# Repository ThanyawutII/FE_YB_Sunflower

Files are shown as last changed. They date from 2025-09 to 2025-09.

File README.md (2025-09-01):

# YB-SUNFLOWER-Future-Engineers🌻✨
### ***We Are Team YB-SUNFLOWER***

</p>
<p align="center">
  
</p>

<p align="center">
 by Yothinburana School

</p>

# Content
`3DModels` This folder includes the 3D design of the vehicle and the rendered model of the vehicle.

`Document (PDF form)` In this folder, we have included a Word document that reorganizes the information from GitHub. It has been converted into a PDF for printing on A4 paper.

`FlowChart` This folder includes diagrams showing the logic and sequence of the robot's control program, highlighting how it processes inputs and controls movements during missions.

`Others` Other essential photos like, work schedule, and robot assemble gif.

`Program` This folder includes all the codes that are used in the WRO 2025 Future Engineers Category and all the programming flowcharts.

`Robot-Photos` This folder contains photos of the vehicle from all perspectives, including side and bottom views.

`Schemes` This folder contains one or more schematic diagrams in JPEG, PNG, or PDF format that depict the electromechanical components of the vehicle. These diagrams illustrate all the elements, including electronic components and motors, and show how they are interconnected.

`Team-Photos` This folder includes photos of the team participating in the WRO 2025 Future Engineers Category.

`Videos` This folder contains YouTube links that show how the robot operates to complete both missions.

`Readme` This Readme contain 3 parts.

  - [About Us](#part-1-about-us)
  - [Mechanical Design](#part-2-mechanical-design)
  - [Obstacle Management](#part-3-obstacle-management)

</p>

# **Part 1: About Us**

## **This is our team.**
Our team name, YB-SUNFLOWER, carries a meaningful story. The word “Sunflower” comes from one of our seniors, Tawan (ตะวัน). In Thai, “sunflower” is ทานตะวัน, which is directly connected to his name. Since 2023, he has inspired us to join the Future Engineers Competition, always supporting us and giving guidance from outside the team. To honor the role he played in motivating us, we included “Sunflower” in our team name. This year is even more special, because for the first time, he is actually competing together with us as part of the team.
 
 <hr>

### **Team History** 
 
 We are **YB-SUNFLOWER**, team from Bangkok, Thailand. We are a part of YB-Robot club from Yothinburana School with our mentor, Punnapon Tanasnitikul. This is our club website https://ybrobot.club/. The club was established in 2009 with the first name being “YB Dream Team”. Last year, we also attend in WRO 2024 that took place in Türkiye.

 This is the first WRO international award in 2010.
  <p align="center">
    
</p>
  </p>
  </p>
This is the second WRO international award in 2011.
 <p align="center">
    
</p>
  </p> 
  </p>

This is the latest WRO international award in 2024 (13th place).  
 <p align="center">
    
</p>
Currently in 2025, we are a part of YB Robot Team. Our senior brought this team name to global recognition, so there is a responsibility since our senior perform excellently. We are hoping to keep this name on the winning streak and make them proud. </p>
  </p>
  </p>
  <hr>

### **Our Team**
   The team consists of 2 intimate friends and 1 of our senior, 'Tawan'. Pawit Nateenantasawasd, Thanyawut Krittikanon, and Natapol Chusang. We have known each other for four years since 2021, forming a strong bond that enhances our collaborative efforts. We first met in high school, being in robot club, competing in many robot competitions together, and sharing our robotic knowledge. Much of what we know today has been learned from the experiences of our seniors in out team, who have taught us valuable lessons and helped shape who we are now.

   Last 2 years, with great enthusiasm and high spirits, we joined Future Engineers twice. Reaching the international round was already a great honor, but we were soon to realize that in order to win, one needs more than just enthusiasm. Our mistakes led us take the 8th and 13th position, a respectable position indeed. 

   This year, we are back with greater confidence, and wiser from past experiences. We honed our strategies and prepared extensively. We fixed every mistake we have done last 2 years. Being back at this competition make us want to ensure the best outcome, and we are here to make everyone proud.  

<p align="center">
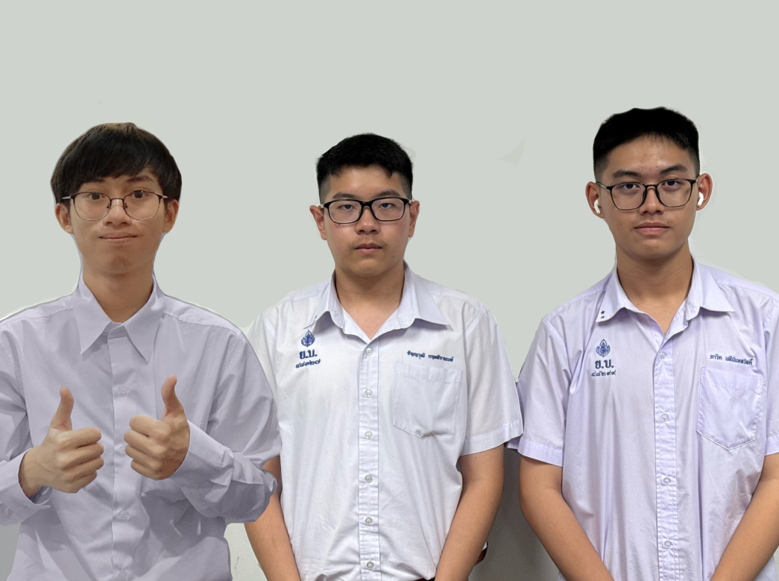
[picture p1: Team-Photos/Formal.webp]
    
</p>

<hr>
There are three members in our team, all extremely focused and dedicated to their positions, performing functions as follows: 
 
#### 1. Thanyawut Krittikanon – Robot Designer
<p align="center">
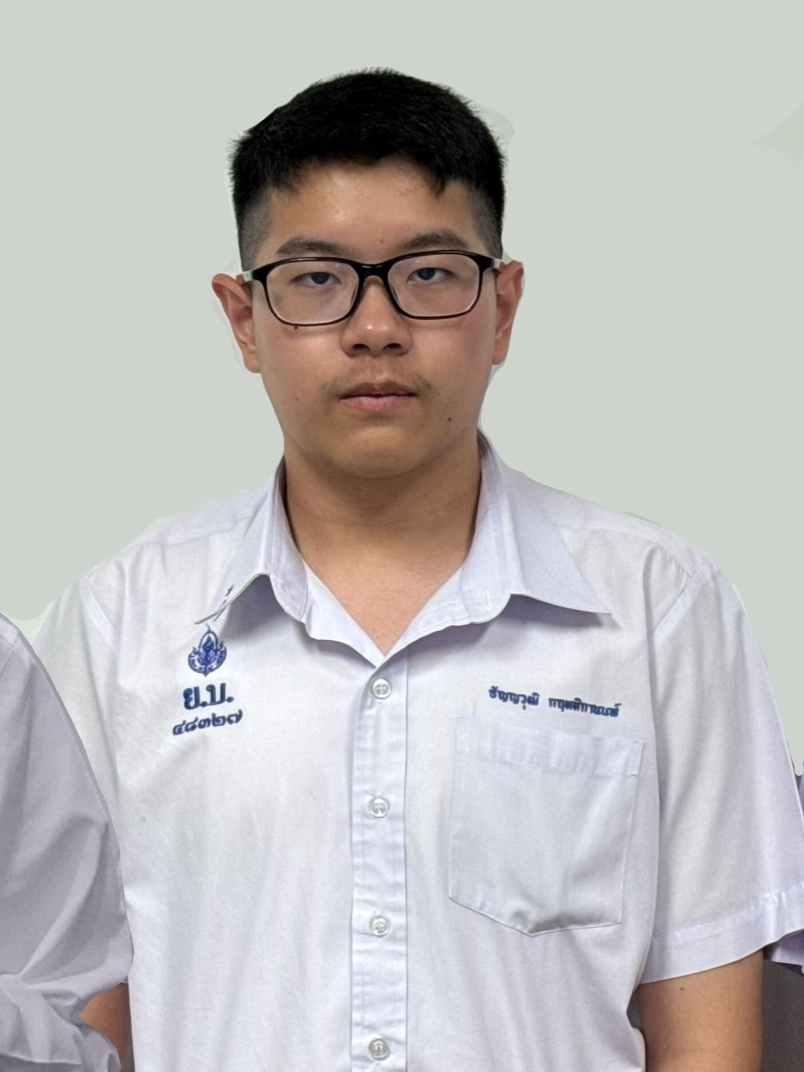
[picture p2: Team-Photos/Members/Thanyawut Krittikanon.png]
    
</p>
Thanyawut is known in our team as **The God of Fusion**, with outstanding skills in 3D design and modeling. His expertise in creating precise and creative robot designs makes him a crucial part of our team. With his talent, he can turn our ideas into detailed models that guide the building process and bring our concepts to life.

#### 2. Pawit Nateenantasawasd – Document Designer and Electrician 
<p align="center">
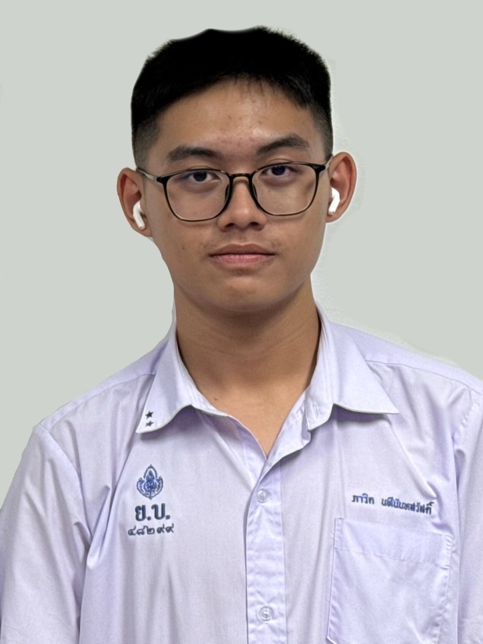
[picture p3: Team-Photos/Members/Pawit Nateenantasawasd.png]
    
</p>
I am Pawit, the document designer of our team. My role is to make sure that everything we present — from reports to presentations — is clear, well-structured, and professional. I enjoy transforming complex ideas into something simple and easy to understand, while also giving it a creative and polished design. Besides designing documents, I also have strong coding skills in multiple languages such as C++, C, Python, Micropython, and HTML, which allow me to contribute to the technical side of our work.

#### 3. Natapol Chusang - Programmer
<p align="center">
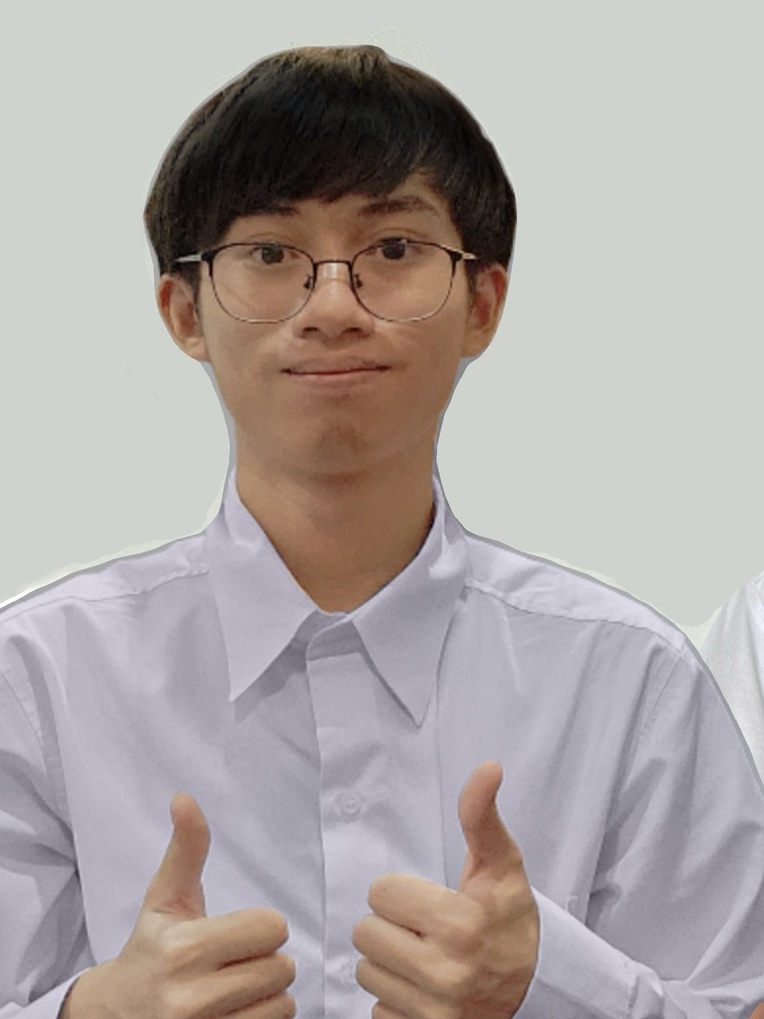
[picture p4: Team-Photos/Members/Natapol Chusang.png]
    
</p>
Natapol is our master programmer, and sometimes we joke that he’s not even human because of how effortlessly he can code anything. From bad-looking robot to advanced systems, he can take on any programming challenge that comes his way. His ability to quickly understand problems and turn them into working solutions makes him a key part of our team’s success. With his skills, even the most complex systems feel possible to build — it’s like there’s no code in the world he cannot write.

</p>
<hr>

### **Our Vision and Goal**

We want to create a robot that can operate similarly to a self-driving car, with the hope of integrating it with an actual automobile. This competition is a step toward our future goal of helping our country and inventing new things. Additionally, via participating in this competition, we have developed and learned numerous skills like collaboration, imagination, and foresight. We also desired to meet new friends in order to exchange knowledge. Furthermore, we intend to utilize the experience we have obtained from this tournament to better ourselves and mentor our junior at school.

<hr>

# **Part 2: MECHANICAL DESIGN**

## Robot's Chassis



The robot chassis design consists mainly of the 3D printed parts, which provide a strong support for all the hardware and electronics devices. Each element is custom-designed to meet our specific requirements and interlocks seamlessly to create a lightweight yet resilient structure. Modification and extension of the orthotics and bambulab 3D-printed chassis is made easily due to its modular construction. It is designed to house the motors, electronic circuitry, and battery while enhancing thermal management and balanced weight distribution for efficient operation. This strategy not only allows for fast modeling and changes in design, but it also makes it easy if an operational change requires that some parts should be removed or replaced with better ones as the robot matures. [All the 3D printable models can be found here](https://github.com/Book2009/Nocturnalist-Future-Engineers/tree/main/3D_Models).

<hr>

### Main Base

<table align="center">
  <tr>
    <td align="center">
      

  <p><a href="https://github.com/Book2009/FE-NOC/blob/main/3D_Models/Main%20Base.stl" target="_blank">Click here to view 3D model.</a></p>
  </tr>
</table>

The main base provides the foundation for creating all other parts. It has cylindrical extensions meant to attach the servo and motor too — designed with LEGO connectors in mind, as opposed to clunky black pegs. Also detailed are the openings to accommodate both differential gear and regular gears so they do not hit the base when trying to rotate. One is a specially designed slot to work with this 3D-printed differential gear mount. The front part is cut out deeper so the servo for steering fits inside and has no problems to spin freely. This design allows to move effectively and optics in the small space of the robot.

<hr>

### Support Base

<table align="center">
  <tr>
    <td align="center">
      

  <p><a href="https://github.com/Book2009/FE-NOC/blob/main/3D_Models/Support%20Plate.stl" target="_blank">Click here to view 3D model.</a></p>
  </tr>
</table>

The purpose of this component is to reinforce the main base securing attachments more firmly. It serves as an additional foundation to mount objects and 3D models, ensuring stability and strength in the overall structure.

<hr>

### C Clip

<table align="center">
  <tr>
    <td align="center">
      

  <p><a href="https://github.com/Book2009/FE-NOC/blob/main/3D_Models/C%20Clip%20x4.stl" target="_blank">Click here to view 3D model.</a></p>
  </tr>
</table>

This component functions as a stabilizing element, similar to a nut, preventing objects from shifting or moving out of place. The open, C-shaped design allows it to be easily positioned around shafts or other components, ensuring they remain securely fixed while maintaining flexibility for adjustments when needed.

<hr>

### Differential Gear Mount

<p align="center">

</p>

<table align="center">
  <tr>
    <td align="center">
      Left
      <p><details>
  <summary>Left Differential Gear Mount</summary>

  <p><a href="https://github.com/Book2009/FE-NOC/blob/main/3D_Models/Left%20Differential%20Gear%20Mount.stl" target="_blank">Click here to view 3D model.</a></p>

</details></p>
    </td>
    <td align="center">
      Right
      <p><details>
  <summary>Left Differential Gear Mount</summary>

  <p><a href="https://github.com/Book2009/FE-NOC/blob/main/3D_Models/Right%20Differential%20Gear%20Mount.stl" target="_blank">Click here to view 3D model.</a></p>

</details></p>
    </td>
  </tr>
</table>

This component is very important for supporting the differential gear firmly and creating solidity to the drivetrain of our robot. Among the basic choices that we made during the work on the robot design, one of the key decisions was to use as few bolts and nuts as possible. This reduction in weight is achieved by using ABS plastic filament instead of steel, which is significantly lighter. This choice not only decreases the overall weight but also simplifies the assembly by requiring fewer additional elements and connections.

<p align="center">


A lighter robot just provides enhanced mobility and more efficiency, which is a crucial factor given the requirements of competitively in the competition. In order to attain a most stringent connection to the main base an interlocking joint was implemented. This design helps in assembling by minimizing the use of conventional fasteners during the construction process. 

<p align="center">
   
  
From this connection, we developed cylindrical formings which work more like bolts, used to place the parts in right position as well as fix them in place.

<p align="center">


Made for added security, precision grooves feature with special C-clips that serve as a replacement for nuts, designed to fit seamlessly. These C-clips are held firmly in place within specially designed grooves that prevent any movement. The groove area has a smaller diameter than the other sections, which ensures a tight fit, preventing any up-and-down motion. The only way to release the C-clip would be to pull it sideways, making the design stable and secure.

<p align="center">


<hr>

### Power Tray

<table align="center">
  <tr>
    <td align="center">
      

  <p><a href="https://github.com/Book2009/FE-NOC/blob/main/3D_Models/Power%20Tray.stl" target="_blank">Click here to view 3D model.</a></p>
  </tr>
</table>

This is the part that holds the 11.1V battery, which is easily removable for charging. This also serves to securely mount the step-down module in place. The raised portion at the back forms a stable platform for mounting the microcontroller board. Hence, this design optimizes the layout by keeping the important electronics of the best organization in space and providing stability.

<hr>

### Servo Bracket

<table align="center">
  <tr>
    <td align="center">
      

  <p><a href="https://github.com/Book2009/FE-NOC/blob/main/3D_Models/Servo%20Bracket.stl" target="_blank">Click here to view 3D model.</a></p>
  </tr>
</table>

This component is intended for firm attachment of a servo motor accompanied by an ultrasonic sensor that is to be used in rotation. The design incorporates cylindrical spigots so as to eliminate the use of black pins which are used to fasten the servo motor fabricated for Lego use. With this arrangement, the sensor movement is stable, well positioned and rigid within the system that improves the overall utility of the sensor.

<hr>

### Camera Plate

<table align="center">
  <tr>
    <td align="center">
      

  <p><a href="https://github.com/Book2009/FE-NOC/blob/main/3D_Models/Camara%20Plate.stl" target="_blank">Click here to view 3D model.</a></p>
  </tr>
</table>

This component is designed to attach to the back of the camera, providing a mounting point that enables it to be securely connected to other components.

<hr>

### Handle
<p align="center">

</p>

<table align="center">
  <tr>
    <td align="center">
      Left
      <p><details>
  <summary>Left Side Handle Support</summary>

  <p><a href="https://github.com/Book2009/FE-NOC/blob/main/3D_Models/Left%20Side%20Handle%20Support.stl" target="_blank">Click here to view 3D model.</a></p>

</details></p>
    </td>
    <td align="center">
      Center
      <p><details>
  <summary>Upper Handle Bracket</summary>

  <p><a href="https://github.com/Book2009/FE-NOC/blob/main/3D_Models/Upper%20Handle%20Bracket.stl" target="_blank">Click here to view 3D model.</a></p>

</details></p>
    </td>
 <td align="center">
      Right
      <p><details>
  <summary>Right Side Handle Support</summary>

  <p><a href="https://github.com/Book2009/FE-NOC/blob/main/3D_Models/Right%20Side%20Handle%20Support.stl" target="_blank">Click here to view 3D model.</a></p>

</details></p>
    </td>
  </tr>
</table>

This handle is an important part as it allows the robot to be safely lifted, especially at times of high speeds. Should it happen that the robot malfunctions or does not act as intended, reaching down quickly to grasp it is practically impossible and could cause unintentional damage by tugging at sensitive pieces, including wires. With the handle, the robot can be raised safely and securely with minimal risk of mishandling.

<hr>

### Gyro-Camara Mount

<table align="center">
  <tr>
    <td align="center">
      

  <p><a href="https://github.com/Book2009/FE-NOC/blob/main/3D_Models/Gyro-Camara%20Mount.stl" target="_blank">Click here to view 3D model.</a></p>
  </tr>
</table>

This component is mounted to the handle and serves as the mounting area for the camera, which is secured through the camera plate. It allows the camera to tilt forward or backward, enabling flexible adjustments to capture the best angle for the robot's operations. Additionally, it offers a stable attachment point for the gyro sensor, ensuring accurate orientation and sensor alignment. The gyro mount is positioned around the middle top of the robot to achieve the most accurate output, while the camera mount is placed at the back to ensure precise object detection.

<hr>

### Steering Module
<p align="center">

</p>

<table align="center">
  <tr>
    <td align="center">
      Left
      <p><details>
  <summary>Bottom Steering Mount</summary>

  <p><a href="https://github.com/Book2009/FE-NOC/blob/main/3D_Models/Bottom%20Steering%20Mount.stl" target="_blank">Click here to view 3D model.</a></p>

</details></p>
    </td>
    <td align="center">
      Center
      <p><details>
  <summary>Steering Linkage Arm</summary>

  <p><a href="https://github.com/Book2009/FE-NOC/blob/main/3D_Models/Steering%20Linkage%20Arm.stl" target="_blank">Click here to view 3D model.</a></p>

</details></p>
    </td>
 <td align="center">
      Right
      <p><details>
  <summary>Top Steering Mount</summary>

  <p><a href="https://github.com/Book2009/FE-NOC/blob/main/3D_Models/Top%20Steering%20Mount.stl" target="_blank">Click here to view 3D model.</a></p>

</details></p>
    </td>
  </tr>
</table>

<table align="center">
  <tr>
    <td align="center">
      Left
      <p><details>
  <summary>Steering Arm</summary>

  <p><a href="https://github.com/Book2009/FE-NOC/blob/main/3D_Models/Steering%20Arm.stl" target="_blank">Click here to view 3D model.</a></p>

</details></p>
    </td>
 <td align="center">
      Right
      <p><details>
  <summary>Steering Arm Support</summary>

  <p><a href="https://github.com/Book2009/FE-NOC/blob/main/3D_Models/Steering%20Arm%20Support.stl" target="_blank">Click here to view 3D model.</a></p>

</details></p>
    </td>
  </tr>
</table>

- #### **Bottom Steering Mount**

Its primary function is to ensure that both steering arms are aligned at the same angle during turns, providing precise and synchronized steering. It connects to the steering linkage arm, which is linked to the servo motor, allowing controlled movement and adjustments to the wheel angles. Additionally, we have designed a mounting point at the front of this component for a light sensor.

- #### **Steering Linkage Arm**

Its main function is to connect to the servo motor and control the steering direction of the robot.

- #### **Top Steering Mount**

Its primary function is to reinforce the bottom steering module, providing additional strength and stability to the steering structure. Additionally, we've designed a mount for an ultrasonic sensor

- #### **Steering Arms**

Its main function is to keep the bottom and top steering mounts aligned with the front of the robot, ensuring stability and correct orientation. Additionally, it serves as the attachment point for the wheels. At the rear of this component, we've designed a large hole to fit a metal standoff or PCB support post, providing extra reinforcement to prevent breakage and enhance durability.
<p align="center">


- #### **Steering Arm Supports**

Its primary function is to provide additional support for the PCB mounting posts, which are made of metal and are insufficiently long.

<hr>

### Chassis

- #### **This is the appearance of chassis to show what our robot looks like without the components.**

<p align="center">


## Components

- #### **3D Printer**: Bambu Lab X1 Carbon by Bambu Lab
<image src="https://github.com/Book2009/FE-NOC/blob/main/Robot-Photos/Robot%20Parts/3D/3D%20Printer.png" width = "400">
The reasons that we use Bambu Lab X1-Carbon 3D printer because this printer is a high-performance 3D printer designed for precision and efficiency. It is equipped with advanced technology and features, making it suitable for professional use as well as hobbyist projects that require high-quality prints.

##### General Specifications

| Specification | Value |
|---|---|
| Build Volume | 256 × 256 × 256 mm³* |
| Nozzle | 0.4 mm Hardened Steel Included |
| Hotend | All-Metal |
| Max Hot End Temperature | 300 ℃ |
| Filament Diameter | 1.75 mm |
| Supported Filament | PLA, PETG, TPU, ABS, ASA, PVA, PET |
| Ideal for | PA, PC, Carbon/Glass Fiber Reinforced Polymer |

##### Build Plate Specifications

| Specification | Value |
|---|---|
| Build Plate Surface | Bambu Textured PEI Plate or Bambu Cool Plate (Pre-installed, Random, Both compatible with Micro Lidar) |
| Max Build Plate Temperature | 110℃@220V, 120℃@110V |

##### Tool Head Specifications

| Specification | Value |
|---|---|
| Max Speed | 500 mm/s |
| Max Acceleration | 20 m/s² |

##### Physical Dimensions

| Specification | Value |
|---|---|
| X1C Dimensions | 389 × 389 × 457 mm³ |
| Package Size (X1C) | 480 × 480 × 535 mm³ |
| Net Weight (X1C) | 14.13 kg |
| Gross Weight (X1C) | 18 kg |
| Package Size (X1C Combo) | 480 × 480 × 590 mm³ |
| Gross Weight (X1C Combo, AMS included) | 22.3 kg |

##### Electrical Requirements

| Specification | Value |
|---|---|
| Voltage | 100-240 VAC |
| Frequency | 50/60 Hz |
| Power Consumption | 1000W@220V, 350W@110V |

<hr>

- #### **Filament** : Acrylonitrile Butadiene Styrene or simply known as ***ABS**
<image src="https://github.com/Book2009/FE-NOC/blob/main/Robot-Photos/Robot%20Parts/3D/ABS%20Filament.png" width = "400">
ABS (acrylonitrile butadiene styrene) is probably the most common filament used in 3D printing. It is especially valuable in strong plastic parts that must remain resilient in the face of temperature swings. It is mainly used in FDM (fused deposition modeling) 3D printers. ABS is a thermoplastic polymer composed of three monomers: acrylonitrile, butadiene, and styrene. The material was first patented in the 1940s and very quickly gained popularity.

<hr><br>

### Movement Parts

- #### **Driving motor** : Power Functions Large-Motor made by LEGO™.
<image src="https://github.com/Book2009/FE-NOC/blob/main/Robot-Photos/Robot%20Parts/Movement/Motor.png" width = "400">
It's a simple motor, and we chose this motor because of its easy connection to our robot and its cost-effectiveness. This motor is small yet powerful and small power consumption. It is the perfect size for our robot comparing to other motor in the market which typically round on all side and need specific mounting bracket for example ZGA32RI. The motor comes with a dedicated port for Lego. So, we modified it to make it able to connect to the board. 

##### Electrical Specifications

| Specification | Value |
|---|---|
| Voltage | 9 V |

##### Mechanical Specifications

| Specification | Value |
|---|---|
| Speed | 390 rpm  |
| Maximum torque | 40 Ncm |

<hr>

- #### **Differential** : Technic, Gear Differential with Inner Tabs and Closed Center, 28 Bevel Teeth
<image src = "https://github.com/Book2009/FE-NOC/blob/main/Robot-Photos/Robot%20Parts/Movement/differential%20gear.png" width = "300"> <image src = "https://github.com/ThanyawutII/Test-2/blob/main/different.jpg" width = "400">

This part ensure that both wheels have the power from the motor, which makes the robot drive forward. This part has gear teeth on the side, which are connected to the gear we put on the motor earlier, and then we put 3 small gears inside the differential. The differential is attached to the main body using an axle from the wheel.

<hr>

- #### **Driving Motor with Differential Gear**
<image src="https://github.com/ThanyawutII/Test-2/blob/main/Screenshot_2024-11-16_223901-removebg-preview.png" width = "500">

After presenting the information and the reasons for selecting the motor and the differential gear, the next crucial step is to understand the outcomes resulting from the connection of these two components. This analysis aims to determine the speed and torque that the system can deliver, which are key factors in optimizing and enhancing the system's performance. Below are the calculation methods and the results derived from our analysis

#### **Step 1: Calculate the gear ratio**
<p>The gear ratio is determined by the ratio of the number of teeth on the input and output gears:</p>
<div class="equation">
    Gear Ratio = <sup>Number of teeth on input gear</sup> / <sub>Number of teeth on output gear</sub> = <sup>36</sup> / <sub>28</sub> = 1.2857
</div>

#### **Step 2: Calculate output RPM**
<p>The output RPM increases due to the gear ratio. To find the output RPM:</p>
<div class="equation">
    Output RPM = Input RPM × Gear Ratio = 390 × 1.2857 = 501.4 RPM
</div>

#### **Step 3: Calculate output torque**
<p>The torque decreases inversely proportional to the gear ratio. To find the output torque:</p>
<div class="equation">
    Output Torque = <sup>Input Torque</sup> / <sub>Gear Ratio</sub> = <sup>40</sup> / <sub>1.2857</sub> = 31.1 N·cm
</div>

#### **Final Results:**
<ul>
    <li><strong>Output RPM</strong>: ~501.4 RPM</li>
    <li><strong>Output Torque</strong>: ~31.1 N·cm</li>
</ul>

</body>
</html>

<hr>

- #### **Servo** : GEEKSERVO 2kg 360 Degrees Servo.
<image src="https://github.com/Book2009/FE-NOC/blob/main/Robot-Photos/Robot%20Parts/Movement/servo.png" width = "400">
We use this servo for steering the robot and employ an ultrasonic sensor for rotation. This servo is compatible with LEGO, making it easy and convenient to build the robot by just putting studs in the hole on the side. We like how you can connect two axles to the dual outputs on this servo so you can power two wheels or gears or mount the servo securely inside articulated limbs and other contraptions. Additionally, the gears inside these servos will 'slip' when the blocking load is too high instead of jamming, helping avoid damage to your servos and boards.

The wires are a standard servo pinout - 
-	Red - positive
-	Brown - negative
-	Yellow - data

##### Electrical Specifications

| Specification | Value |
|---|---|
| Working voltage | 3.3V~6V  |
| Rated voltage | 4.8V |
| Rated current | 200mA |
| Stall current | 700mA |
| Sliding current | 450mA |

<hr>

- #### **Front Wheel** : Lego Tire 43.2 x 22 ZR and Wheel 30.4mm D. x 20mm with No Pin Holes and Reinforced Rim
<image src = "https://github.com/ThanyawutII/Test/blob/main/Screenshot_2024-10-23_143240-removebg-preview.png" width = "200"> <image src = "https://github.com/ThanyawutII/Test/blob/main/56145-removebg-preview%20(1).png" width = "200">
  
  - #### **Rear Wheel** : Lego Tire 49.6 x 28 VR and Wheel 36.8mm D. x 26mm VR with Axle Hole
<image src = "https://github.com/ThanyawutII/Test-2/blob/main/S__5021716-removebg-preview.png" width = "200"> <image src = "https://github.com/ThanyawutII/Test-2/blob/main/S__5021714-removebg-preview.png" width = "200">

There are a lot of wheels to select. We chose this one because of it's size. If the wheels are too small, it reduces the speed due to the lack of rotation. But if the wheels are too big, it makes the robot slower and harder to control. With the combination of the motor and the wheels, the robot can maintain the speed we can control.

<hr><br>

### Controller

- #### **Microcontroller Board** : Arduino Mega 2560 R3

This part is like a brain of our body. Its job is to store all the program of our robot from the computer, every component in the robot comes through here. We chose this board because of its connection port, it contains tons of ports that we want such as 3 UART port. We used Arduino Uno last year, but the problem is there's not enough port for OpenMV and GY-25. But there's some disadvantage in this board. Because this board has a lot of connection port, it comes with weight and size. It's almost 2 times longer than the UNO. And that makes the robot long and heavy.

| Specification | Value |
|---|---|
| Microcontroller | ATmega2560 |
| Operating Voltage | 5V |
| Input Voltage (recommended) | 7-12V |
| Input Voltage (limit) | 6-20V |
| Digital I/O Pins | 54 (15 provide PWM output) |
| Analog Input Pins | 16 |
| DC Current per I/O Pin  | 20 mA |
| DC Current for 3.3V Pin | 50 mA |
| Flash Memory | 256 KB (8 KB used by bootloader) |
| SRAM | 8 KB |
| EEPROM | 4 KB |
| Clock Speed | 16 MHz |
| LED_BUILTIN | 13 |
| Length | 101.52 mm |
| Width | 53.3 mm |
| Weight | 37 g |

Additional information about UART:
UART operates by transmitting data as a series of bits, including a start bit, data bits, an optional parity bit, and stop bit(s). Unlike parallel communication, where multiple bits are transmitted simultaneously, UART sends data serially, one bit at a time. As the name reveals the protocol operates asynchronous which means that it doesn't rely on a shared clock signal. Instead, it uses predefined baud rates to determine the timing of data bits.



Our robot has serial1 and serial3, serial1 is connected to compass while serial3 is connected to OpenMV camera. They are connected to the UART port on the Arduino mega.

<hr>

- #### **Sensor Shield** : Gravity IO Sensor Shield for Arduino Mega Due

This part is an extension of the board. It is where ultrasonic, light sensors, button sensors, camera, compass, and servos go. It has a lot of connection pin which can be used for each component. But with that it also come with a very long design. Make it hard to design where to place it on robot.

| Specification | Value |
|---|---|
| Compatibility | Most Arduino shields |
| Compatible Boards | Arduino Mega boards, DFRobot megaADK, Arduino megaADK |
| Extended TTL Connection Pins | Four Serial ports |
| Prototyping Area | DIP prototyping area for additional modules or components |
| Xbee Slots | 3 |
| microSD Slot | 1 |
| Power Switch | Between Arduino Mega or external power |
| Size | 125 x 57 mm (4.92 x 2.24") |

<hr>

- #### **Motor Shield** : Gravity 2x2A Motor Shield for Arduino Twin

This part is also an extension of the board. It makes the connection between the board and motor easier. We connect the pin with the top of sensor shield.

| Specification | Value |
|---|---|
| Motor Driven Voltage | 4.8V to 35V |
| Output Current | Up to 2A/channel |
| Total Power Dissipation | 25W (T=75℃) |
| Driven Structure | Dual full-bridge driver |
| Driven Power Port | External power terminal, or VIN from Arduino |
| Driven Output Port | 2 channel screw terminals, or male PIN headers |
| Control Port | 4 TTL compatible digital signals (Digital 10-13) |
| Operation Temperature | -25℃ to 130℃ |
| Shield Size | 56x57mm (2.20x2.24") |

<hr><br>

### Power Management And Inspection
- #### **Camera** : OpenMV H7 R1
<image src="https://github.com/Book2009/FE-NOC/blob/main/Robot-Photos/Robot%20Parts/Power%20Management%20And%20Inspection/OpenMV%20Camera.png" width = "400">
This component is very important for avoiding obstacle. It can detect red and green obstacle from distance to avoid crashing into it. The OpenMV also comes with its own microcontroller. Making the robot locate and think faster when see the obstacle. The OpenMV also comes with GLCD screen at the back of it to display what the camera sees. This camera can be coded with MicroPython. Additionally, this camera wires are connected with the sensor shield.

##### STM32H743VI Specifications

| Specification | Value |
|---|---|
| **Processor** | STM32H743VI ARM Cortex M7 |
| **Clock Speed** | 480 MHz |
| **SRAM** | 1 MB |
| **Flash Memory** | 2 MB |
| **I/O Voltage** | 3.3V (5V tolerant) |
| **Number of I/O Pins** | 10 |

##### Interfaces

| Specification | Value |
|---|---|
| **USB** | Full-speed USB (12 Mbps) interface |
| **μSD Card Socket** | Capable of 100 Mbps read/write |
| **SPI Bus** | Up to 80 Mbps |
| **I2C Bus** | Up to 1 Mbps |
| **CAN Bus** | Up to 1 Mbps |
| **Asynchronous Serial Bus** | Up to 7.5 Mbps |

##### Analog

| Specification | Value |
|---|---|
| **ADC** | 12-bit |
| **DAC** | 12-bit |

##### Control

| Specification | Value |
|---|---|
| **Servo Control Pins** | 3 I/O pins |
| **Interrupts and PWM** | Available on all I/O pins |

##### LEDs

| Specification | Value |
|---|---|
| **RGB LED** | Yes |
| **High Power IR LEDs** | Two 850nm |

##### Camera Module

| Specification | Value |
|---|---|
| **Default Sensor** | OV7725 |
| **Resolution** | 640x480 |
| **Modes** | 8-bit Grayscale at 75 FPS, 16-bit RGB565 (75 FPS above 320x240, 150 FPS below 320x240) |
| **Lens** | 2.8mm, M12 mount |
| **Additional Modules** | Global Shutter Camera, FLIR Lepton Adapter |

##### Power

| Specification | Value |
|---|---|
| **Battery Connector** | Compatible with 3.7V LiPo batteries |

  <hr>

- #### **Ultrasonic sensor** : Gravity URM 09 ultrasonic distance sensor.
<image src="https://github.com/Book2009/FE-NOC/blob/main/Robot-Photos/Robot%20Parts/Power%20Management%20And%20Inspection/Ultrasonic.png" width = "400">
  
An Ultrasonic sensor is a device that can measure the distance to an object by using sound waves. It measures distance by sending out a sound wave at a specific frequency and listening for that sound wave to bounce back.

Since it is known that sound travels through air at about 344 m/s (1129 ft/s), you can take the time for the sound wave to return and multiply it by 344 meters (or 1129 feet) to find the total round-trip distance of the sound wave. Round-trip means that the sound wave traveled 2 times the distance to the object before it was detected by the sensor; it includes the 'trip' from the sonar sensor to the object AND the 'trip' from the object to the Ultrasonic sensor (after the sound wave bounced off the object). To find the distance to the object, simply divide the round-trip distance in half.

DFRobot URM09 is an ultrasonic sensor specially designed for fast ranging and obstacle avoidance applications. Its measuring frequency can reach up to 30Hz. The sensor adopts built-in temperature compensation and analog output. Meanwhile, it can provide accurate distance measurement within 500 cm. The sensor is compatible with Arduino, Raspberry Pi, or other main controllers.

<p align="center">


<p align="center">


We use the Ultrasonic Sensor (SEN0307) to measure the distance between the robot and the walls. This sensor utilizes an analog voltage output and provides accurate distance measurements within the range of 2-500 cm, with a precision of 1 cm and an accuracy of ±1%. It is highly suitable for this competition and is compatible with boards that have 3.3V or 5V logic levels.

##### Electrical Specifications

| Specification | Value |
|---|---|
| Supply Voltage | 3.3~5.5V DC |
| Operating Current | 20mA |

##### Performance Specifications

| Specification | Value |
|---|---|
| Operating Temperature Range | -10°C to +70°C |
| Measurement Range | 2cm to 500cm (can be set) |
| Resolution | 1cm |
| Accuracy | 1% |
| Frequency | 50Hz Max |

<hr>

- #### **Light Sensor** : ZX-03B and ZX-03R By INEX

ZX-03B

<image src = "https://github.com/ThanyawutII/Test/blob/main/fc679f07ebcded1ab267a5d197fac817-removebg-preview.png" width = "300">

ZX-03R

<image src = "https://github.com/ThanyawutII/Test/blob/main/Screenshot_2024-10-23_152022-removebg-preview.png" width = "300">

The color sensors play an important role in both rounds, as we use them for line detection. There are 2 lines with different colors in the corner of the race field, which is why we use 2 different colors of the color sensor, blue and red. The blue color sensor is used for detecting both colors, while the red color sensor is only used for the blue line.

<hr>

- #### **Gyro/Compass** :GY-25
A gyro is a component that enables a robot to determine its orientation and turn in the appropriate direction. We chose this gyro sensor specifically because of how effective it is. It also comes in a very small
size to attach to our robot.

<image src = "https://github.com/Book2009/FE-NOC/blob/main/Robot-Photos/Robot%20Parts/Power%20Management%20And%20Inspection/Compass.png" width = "400">

##### Power and Communication

| Specification | Value |
|---|---|
| Power supply | 3-5V (internal low dropout regulator) |
| Used Chip | MCU+MPU6050 |
| Communication mode | Serial communication (baud 9600, 115200), IIC communication |
| Operating Current | 15 mA |

##### Angular Measurement

| Specification | Value |
|---|---|
| Angular Resolution | 0.01° |
| Direct Data | YAW ROLL PITCH |
| Measuring range of axes | -180 to +180 degrees |
| Resolution | 0.01 degrees |
| Frequency Response | 100Hz (115200bps) |
| Operating Temperature | -20 to 85°C |

<hr>

- #### **Touch Sensor** : ZX-Switch01 by INEX
This button gives us an easier way to start the robot. Since the controller board doesn't come with switches. So, we found this button that could be attached to the frame outside the board using bolt. 



<hr>

- #### **On/Off Switch** : SPST ON/OFF Switch 2 Pin Rocker Switch DC 125/250V
This switch is for cutting the power from the battery to the robot. The regulation states that before starting the robot, the power must be cut off. That's when this switch came in. To use this switch, we solder red wire (Positive pole) to the switch on 1 side for input. Then another solder red wire for output on the opposite side. You can put the black wire (Negative pole) straight into the step-down. When the switch is turned on, the power from the battery will direct into the stepdown and then the robot. Additionally, we have designed a protective case for this switch to ensure safety and durability. [You can view the 3D model here](https://github.com/Book2009/FE-NOC/blob/main/3D_Models/Switch%20Box.stl).



<hr>

- #### **Step-down** : HW-360 V6.0
This is a step-down DC-DC module. It comes with a status indicator light, a display screen that shows the voltage meter, and self-calibration of the voltage meter. The electrical voltage has an error of 0.05 V, with a measuring range of 0–40 V. We need this step down to show us how long until we need to recharge the battery.



##### Input

| Specification | Value |
|---|---|
| Input voltage | DC 4.0 ~ 38V |

##### Output

| Specification | Value |
|---|---|
| Output voltage | DC 1.25V ~ 36V continuously adjustable |
| Output current | Max 5A |
| Output power | Up to 75W |

##### Measurements

| Specification | Value |
|---|---|
| Voltmeter error | ± 0.05V |
| Measure range | 0 ~ 40V |

##### Performance

| Specification | Value |
|---|---|
| Conversion efficiency | Up to 96% |
| Load regulation | S (I) ≤ 0.8% |
| Voltage Regulation | S (u) ≤ 0.8% |

<hr>

- #### **Battery** : 11.1 voltage 3 cell Lipo-Battery.
<image src="https://github.com/ThanyawutII/Test/blob/main/Screenshot_2024-10-22_112329-removebg-preview.png" width = "400">
We upgraded from a 7.4V battery to an 11.1V battery due to reliability concerns and the limited capacity of the 7.4V option. The 11.1V battery enhances the robot's performance by providing higher voltage, which reduces current draw and minimizes power losses during operation. This upgrade ensures stable and continuous functionality without significant voltage drops, even under high current loads, a critical factor during intense practice sessions and competitions.

To ensure compatibility with our motor's maximum voltage rating of 9V, we incorporated a step-down voltage regulator. This module efficiently converts the 11.1V input to a stable 9V output, maintaining the motor's safety while maximizing the extended runtime afforded by the 11.1V battery. This solution not only improves reliability but also instills confidence in the system's durability and performance under demanding conditions.

##### Specification

| Specification | Value |
|---|---|
| 3 cells Voltage | 11.1V |
| Capacity | 1300mAh 20C |
| Charging Current | Up to 5 times the capacity (5C) |
| Connectors | Dean type, easily disconnectable |

<br><hr>

### Robot

- #### **This is the appearance of our robot in real life to show what our robot looks like with the components.**
<p align="center">

</p>

- #### **It shows the inside of the robot, detailing where and how to place everything.**
<p align="center">
    

<br><hr>

### Wiring Diagram and Power Distribution Diagram
- #### **It shows you the connection of various components to the microcontroller.**
<p align="center">
    

- #### **It shows the ports of various components connected to the microcontroller, as well as the voltage levels supplied to the microcontroller and its connected components.**
<p align="center">
    

<br><hr>

# **Part 3: Obstacle Management**

### **How the robot works (Youtube Link)**

To help you better understand what I'm explaining, you can [click here](https://youtu.be/qQTfzTyW7DM) to view the video we created.

<div align="center">
  <a href="https://www.youtube.com/watch?v=qQTfzTyW7DM">
    
  </a>
</div>

## Open Challenge round

In this round, our robot must complete three(3) laps on the track with random placements of the inside track walls within 3 minutes.

### **Open Challenge round (Youtube Link)**

This video shows our robot completing the first round(Open Challenge), you can [click here](https://youtu.be/8S626QcRaPA) to view the video we created.

<div align="center">
  <a href="https://www.youtube.com/watch?v=8S626QcRaPA">
    
  </a>
</div>

### **The strategy**

In this Open Challenge round, the robot will use the ultrasonic to measure the distance of the robot from the outer wall. The robot will use the color sensor to check the line color. If the first color is red, the robot will turn right, and if it’s blue, the robot will turn left(because if the robot has to turn right, it will detect the red line first, and if it has to turn left, it will detect the blue line first, using different color sensors for detecting each line color). Every time, the robot will check how many times it has crossed the first line. It will count 12 lines(1 round = 4 lines), and after that, it will walk with the timer that we set until the time we set runs out.

<p align="center">
If the first line is red
</p>

<table align="center">
  <tr>
    <td align="center">
      Left
      <p>Start</p>
    </td>
    <td align="center">
      Right
      <p>When detect the first line</p>
    </td>
  </tr>
</table>

<p align="center">
If the first line is blue
</p>

<table align="center">
  <tr>
    <td align="center">
      Left
      <p>Start</p>
    </td>
    <td align="center">
      Right
      <p>When detect the first line</p>
    </td>
  </tr>
</table>

The robot will use the distance of robot from the wall and gyro sensor degree to саlculate into steering degree (turning degree) to maintain the distance between the wall with PID (Proportional Integral Derivative) 

<p> 
U(t) = k<sub>p</sub> e(t) + k<sub>i</sub_ [ e(t) dt + k<sub>d</sub> (de/dt) 
</p> 
<p>(PID Formula) 
</p>

<br><hr>

### **Flowchart**

<image src="https://github.com/ThanyawutII/Test/blob/main/OpenChallengeMain%20(1).jpg" height = "600">

<hr>

### **Source Code**

- #### **Section 1 [Open Challenge round]**

```c++
#include <Mapf.h>
#include <PID_v2.h>
#include <Wire.h>
#include <Servo.h>

Servo myservo;
Servo myservo2;

const int E1Pin = 10;
const int M1Pin = 12;

/**inner definition**/
typedef struct {
  byte enPin;
  byte directionPin;
} MotorContrl;

const int M1 = 0;
const int MotorNum = 1;

const MotorContrl MotorPin[] = { { E1Pin, M1Pin } };

const int Forward = LOW;
const int Backward = HIGH;

//Button
int BUTTON = A8;

//PID
PID_v2 compassPID(0.7, 0.0001, 0.05, PID::Direct);

//Ultra
int const ULTRA_PIN = A9;
int const ULTRA_PIN_II = A10;

//INEX Gyro
float pvYaw;
uint8_t rxCnt = 0, rxBuf[8];

//  Light Sensors
int const RED_SEN = A6;
int const BLUE_SEN = A7;

// Servo
int const STEER_SRV = 27;  //16
int const ULTRA_SRV = 25;  //23

//Others
char TURN = 'U';
long halt_detect_line_timer;
int Line_Number = 0;
int plus_degree = 0;
int count;
```
This code sets up a robot with servos, motors, sensors (light, ultrasonic, and gyro), and a PID controller for compass-based movement. It configures motor pins, light sensor pins, and controls turn direction and line detection timing to guide the robot's navigation.

- #### **Section 2 [Open Challenge round]**

```c++
void setup() {
  // put your setup code here, to run once:
  Serial.begin(9600);
  Serial1.begin(9600);
  compassPID.Start(0, 0, 0);
  compassPID.SetOutputLimits(-180, 180);
  compassPID.SetSampleTime(10);
  pinMode(STEER_SRV, OUTPUT);
  pinMode(ULTRA_SRV, OUTPUT);
  pinMode(ULTRA_PIN, INPUT);
  pinMode(RED_SEN, INPUT);
  pinMode(BLUE_SEN, INPUT);
  pinMode(BUTTON, INPUT);
  initMotor();
  while (!Serial)
    ;
  myservo.attach(ULTRA_SRV, 500, 2400);
  myservo2.attach(STEER_SRV, 500, 2500);
  steering_servo(0);
  ultra_servo(0, 'L');
  // check_leds();
  while (analogRead(BUTTON) > 500)
    ;
  zeroYaw();
}
```
The setup function initializes serial communication, PID control, motor, servo pins, and sensors. It calibrates the compass with `zeroYaw()`, waits for a button press, and prepares the system for operation by attaching servos and starting the PID control.

- #### **Section 3 [Open Challenge round]**

```c++
void loop() {
  float baseDesiredDistance = 25;
  while (analogRead(BUTTON) > 500) {
    getIMU();
    motor(50);
    Color_detection();
    float desiredDistance = baseDesiredDistance;  // Start with the base value
    if (TURN == 'L') {
      desiredDistance = 16;
    } else if (TURN == 'R') {
      desiredDistance = 17.5;
    }
    float distanceError = getDistance() - desiredDistance;
    float deadband = 2.0;
    if (abs(distanceError) < deadband) {
      distanceError = 0.0;
    }
    float directionFactor = (TURN == 'R') ? -1.0 : 1.0;
    float adjustedYaw = pvYaw - (distanceError * directionFactor);
    float pidOutput = compassPID.Run(adjustedYaw);
    steering_servo(pidOutput);
    ultra_servo(pvYaw, TURN);
    // Serial.println(getDistance());

    if (count >= 12) {
      long timer01 = millis();
      while (millis() - timer01 < 800) {
        motor(100);
        getIMU();
        Color_detection();
        float desiredDistance = baseDesiredDistance;  // Start with the base value
        if (TURN == 'L') {
          desiredDistance = 12;
        } else if (TURN == 'R') {
          desiredDistance = 14.5;
        }
        float distanceError = getDistance() - desiredDistance;
        float deadband = 2.0;
        if (abs(distanceError) < deadband) {
          distanceError = 0.0;
        }
        float directionFactor = (TURN == 'L') ? -1.0 : 1.0;
        float adjustedYaw = pvYaw + (distanceError * directionFactor);
        float pidOutput = compassPID.Run(adjustedYaw);
        steering_servo(pidOutput);
        ultra_servo(pvYaw, TURN);
      }
      motor(0);
      while (true) {
      }
    }
  }
  motor(0);
  while (analogRead(BUTTON) <= 500) {
  }
  while (analogRead(BUTTON) > 500)
    ;
  while (analogRead(BUTTON) <= 500)
    ;
}
```
The loop function controls the robot's movement by reading sensor values, adjusting motor speed, and steering using PID feedback. It checks the button status to start/stop, adjusts the robot's direction based on distance errors, and uses servos to steer. When a specific count is reached, it stops.

<br><hr>

## Obstacle Challenge round

In this round, our robot must complete three laps on a track marked with randomly placed green and red traffic signs.
<br>
● Red Obstacle: Keep to the right side of the lane.
<br>
● Green Obstacle: Keep to the left side of the lane.
<br>
The robot must not move any traffic signs. After finishing the three laps, the robot must find a parking lot and perform parallel parking.

### **Obstacle Challenge round(Youtube Link)**

This video shows our robot completing the Second round(Obstacle Challenge), you can [click here](https://youtu.be/9oGPSgff0DQ) to view the video we created.

<div align="center">
  <a href="https://www.youtube.com/watch?v=9oGPSgff0DQ">
    
  </a>
</div>

### **The strategy**

In the WRO 2024 Obstacle Challenge round, the robot uses a combination of ultrasonic sensors, a color sensor, a gyro, and an OpenMV Camera to navigate the course, detect and avoid obstacles, and maintain a safe distance from walls. The OpenMV Camera identifies obstacles and their colors, turning right for red obstacles and left for green ones, while the gyro ensures smooth and precise turns.

After completing the second round, the robot uses the OpenMV Camera to search for the purple parking area by detecting its color and comparing its size to the red and green pillars to determine its location. Once the third round is complete, the robot proceeds to park in the identified purple parking area, accurately positioning itself based on the location recorded by the OpenMV Camera.

<br>

<p align="center">
If the robot sees red obstacle
</p>

</p>
<p align="center">
  
</p>

<br>

<p align="center">
If the robot sees green obstacle
</p>

</p>
<p align="center">
  
</p>

The robot still uses the PID to walk, but we added the avoidance degree to avoid the obstacles.

<br>

<p align="center">
After completing the second round
</p>

</p>
<p align="center">
  
</p>

The robot uses the OpenMV Camera to search for the purple parking area, detecting its color directly and comparing its size to the red and green pillars to determine its position.

<br>

<p align="center">
Park in parking area
</p>

</p>
<p align="center">
  
</p>

The robot will drive to park in the purple parking area that was detected, using the stored position to accurately align itself.

<br><hr>

### **Flowchart**

<image src="https://github.com/ThanyawutII/FE_YB_Sunflower/blob/main/FlowChart/ObstecleChallenge.jpg" height = "650">

<hr>

### **Source Code**

- #### **Section 1 [Obstacle Challenge round]**

```c++
#include <Mapf.h>
#include <PID_v2.h>
#include <Servo.h>
#include "CameraHandler.h"
```
We declare essential libraries for robot control: `Mapf.h` for Mapping the constrained distance from one range to another, `PID_v2.h` for smooth movement control, `Servo.h` for servo motor positioning, and `CameraHandler.h` for processing camera data. These libraries enable the robot to navigate, adjust movement, and interpret visual information effectively.

- #### **Section 2 [Obstacle Challenge round]**

```c++
CameraHandler camera;
BlobData blob;
BlobData purple_blob1;
BlobData purple_blob2;
```
We initialize a `CameraHandler` object called camera to manage the camera’s functions. It also creates three `BlobData` instances: `blob` for storing red and green pillar information, and `purple_blob1` and `purple_blob2` specifically for tracking two separate purple blobs. These variables enable the robot to detect, distinguish, and interact with multiple objects in its environment, particularly purple-colored ones.

- #### **Section 3 [Obstacle Challenge round]**

```c++
Servo myservo;
Servo myservo2;
```
We declare two Servo objects, `myservo` and `myservo2`, allowing control of two individual servo motors.

- #### **Section 4 [Obstacle Challenge round]**

```c++
const int E1Pin = 10;
const int M1Pin = 12;

typedef struct {
  byte enPin;
  byte directionPin;
} MotorContrl;

const int M1 = 0;
const int MotorNum = 1;

const MotorContrl MotorPin[] = { E1Pin, M1Pin };

const int Forward = LOW;
const int Backward = HIGH;
```
We set up motor control using `E1Pin` and `M1Pin` for power and direction. The `MotorContrl` structure and `MotorPin` array organize these pins, while Forward and Backward constants control motor rotation, making direction easy to manage.

- #### **Section 5 [Obstacle Challenge round]**

```c++
int const RED_SEN = 6;
int const BLUE_SEN = 7;
int const BUTTON = 8;
int const ULTRA_PIN = 9;
int const ULTRA_PIN_II = 10;
int const STEER_SRV = 27;
int const ULTRA_SRV = 25;
```
We connect Red sensor to port 6, Blue sensor to port 7, Button to port 8, Ultrasonic that measure distance between robot and the wall to port 9, Ultrasonic in front of the robot to port 8+10, Servo for steering port 27, and the last one, Servo for turning ultrasonic port 25.

- #### **Section 6 [Obstacle Challenge round]**

```c++
float pvYaw;
uint8_t rxCnt = 0, rxBuf[8];
```
We define `pvYaw` as a float to store the robot's yaw (orientation) angle. `rxCnt` is an 8-bit integer to count received data, and `rxBuf` is an 8-byte array to hold incoming data.

- #### **Section 7 [Obstacle Challenge round]**

```c++
long halt_detect_line_timer = 0;
long halt_detect_parking = 0;
long MV_timer = 0;

float found_parkAngle = 0;
float absYaw;
float uturnYaw;
float avoidance_degree;

int last_found_signature;
int plus_degree = 0;
int count_line = 0;
int parking_step = 0;
int parkingsection = -1;
int side = 1;
int hi = 0;
int angle = 115;

bool startpark = false;
bool parking = false;
bool next = false;
bool foundpark = false;
bool uturn = false;

char currentBlock = 'N';
char previousBlock = 'N';
char lastblock;
char lastfound = 'U';
char TURN = 'U';
char ULTRA_DIR = 'R';
```
This code above, we define several variables used for various control and tracking functions. `long` is used for defining time variable. `float` for variable that has decimal. `int` for variable that is integer. `bool` for variable that its output is true and false. `char` is for variable that is used to store data as a single character.

- #### **Section 8 [Obstacle Challenge round]**

```c++
void setup() {
  initialize_everything();
  while (analogRead(BUTTON) > 500)
    ;
  zeroYaw();
}
```
In `void setup` we initialize every part of our robot (function mentioned in another page) and then wait until the button is pressed. After that, reset the compass.

- #### **Section 9 [Obstacle Challenge round]**

```c++
void loop() {
  // Calculate camera errors
  camera.handleIncomingData();
  BlobData tempBlob = camera.getBlobData();
  if (tempBlob.signature == 1) {
    // RED
    last_found_signature = 1;
    blob = tempBlob;

  } else if (tempBlob.signature == 2) {
    // GREEN
    last_found_signature = 2;
    blob = tempBlob;

  } else if (tempBlob.signature == 3) {
    purple_blob1 = tempBlob;
  } else if (tempBlob.signature == 4) {
    purple_blob2 = tempBlob;
  }
```
This code processes data from the camera to identify and sort detected blobs by color. It first updates the camera data, then retrieves the current blob as `tempBlob`. The code checks the color of `tempBlob` based on its "signature": if it’s red (1), it sets `last_found_signature` to 1 and stores `tempBlob` as blob. If it’s green (2), it does the same but sets `last_found_signature` to 2. Purple blobs are handled separately, with `purple_blob1` storing blobs marked as 3 and `purple_blob2` storing blobs marked as 4.

- #### **Section 10 [Obstacle Challenge round]**

```c++
 float avoidance_degree = 0;
  if (tempBlob.signature == 3 && tempBlob.width / 3.9 > blob.width) {
    avoidance_degree = calculate_avoidance(tempBlob.signature, tempBlob.width, tempBlob.x, tempBlob.y) * -2;
  } else {
    avoidance_degree = calculate_avoidance(blob.signature, blob.width, blob.x, blob.y);
  }
```

In this code, `avoidance_degree` is set to 0 at the start. The code then checks if `tempBlob` has a signature of 3 (meaning it’s a purple blob) and if it’s wider than the main blob divided by 3.9. If both are true, it calculates an avoidance angle using `tempBlob`’s data and multiplies it by -2 to create a stronger reaction in the opposite direction. If the conditions aren’t met, it calculates a normal avoidance angle using red and green blob's data instead.

- #### **Section 11 [Obstacle Challenge round]**
```c++
  int desiredDistance = parking_step == 0 ? (camera.isBlockFound() ? 20 : 40) : 15;
  float distanceError = getDistance() - desiredDistance;
  float frontDistance = getDistanceII();

  float deadband = 2.0;
  if (abs(distanceError) < deadband) {
    distanceError = 0.0;
  }
  float directionFactor = (ULTRA_DIR == 'R') ? -1.0 : 1.0;
  float adjustedYaw = pvYaw - clamp(distanceError * directionFactor, -20, 20);
  float pidOutput = compassPID.Run(adjustedYaw);
```
From code above, we declare variables called `desireDistance` to set the perfect distance between the robot and wall. If parking step is not equal to 0 (it exits the main loop and going to perform parking) and it sees a block, set the `desireDistance` to 20 if not set to 40, and if it is in the main loop set it to 15. `distanceError` is to make the robot know that is it too far from `desireDistance`. deadband is to neglect small error. If `distanceError` is less than 2 then ignore them. Because we make the ultrasonic move left and right due to the block nearest to the robot, we need to add `directionFactor` to let the robot keep distance from the wall normally. The `adjustedYaw` is calculated by adjusting `pvYaw` using the `distanceError` and `directionFactor`, clamped between -20 and 20. Finally, the `pidOutput` is calculated using the `compassPID` controller to adjust the robot's steering.

- #### **Section 12 [Obstacle Challenge round]**

```c++
  // TEST PARKING

  if (count_line >= 8 && count_line < 12 && tempBlob.signature == 3 && parkingsection == -1) {
    parkingsection = count_line % 4;
  } else if (count_line > 12) {
    if (parkingsection == 0) {
      parkingsection = 4;
    }
  }
```
We tell the robot to find the parking lot while it's in the third lap. After it found the parking lot, divide the variable `count_line` by 4 then you get the remainder. That's the section of the field that the robot's in at the time. Store it in `parkingsection`. If `parkingsection` equal to 0, change that to 4 to ensure that the robot park smoothly.

- #### **Section 13 [Obstacle Challenge round]**

```c++
if (parking_step == 1) {
    ULTRA_DIR = TURN == 'R' ? 'L' : 'R';
  }
```
While the robot searching for parking lot, change side that ultrasonic heads to. So, the ultrasonic scan outside wall.

- #### **Section 14 [Obstacle Challenge round]**

```c++
int parking_degree = ((purple_blob1.x + purple_blob2.x) / 2 - 160) * -0.5;
  int final_degree = camera.isBlockFound() ? mapf(min(max(getDistance(), 15), desiredDistance), 15, desiredDistance, pidOutput, avoidance_degree) : pidOutput;
```
`parking_degree` is the variable that calculate degree of steering wheel for the robot to go into parking lot safely. `final_degree` is the variable that calculate the degree of steering wheel throughout the round. If it sees a block, avoid them. If it doesn't see anything, just continue using distance from the wall and compass.

- #### **Section 15 [Obstacle Challenge round]**

```c++
 getIMU();
  color_detection();
```
This is the beginning, first, get compass value. Then, start detecting the first color of the line on the field after the robot start.

- #### **Section 16 [Obstacle Challenge round]**

```c++
 switch (parking_step) {
    case 1:

      if (!startpark) {
        halt_detect_parking = millis();
        startpark = true;
      }
      if (tempBlob.signature != 3 && purple_blob1.width < 70) {
        steering_servo(pidOutput);
        ultra_servo(pvYaw, ULTRA_DIR);
        motor(40);
      } else {
        parking_step = 2;
        startpark = false;
      }
      break;
    case 2:
      halt_detect_line_timer = millis();
      if (!startpark) {
        halt_detect_parking = millis();
        startpark = true;
      }
      if (millis() - halt_detect_parking < 1400) {
        steering_servo(final_degree);
        ultra_servo(0, ULTRA_DIR);
        motor(40);
      } else {
        parking_step = 3;
        startpark = false;
        if (TURN == 'L') {
          plus_degree += 90;
        } else {
          plus_degree -= 90;
        }
      }

      break;

    case 3:

      if (!startpark) {
        halt_detect_parking = millis();
        startpark = true;
      }
      if (millis() - halt_detect_parking < 2000) {
        steering_servo(pvYaw);
        ultra_servo(0, ULTRA_DIR);
        motor(-40);
      } else {
        parking_step = 4;
        startpark = false;
      }

      break;

    case 4:
      if (frontDistance > 10) {
        steering_servo(mapf(clamp(frontDistance, 10, 20), 20, 10, parking_degree, 0));
        motor(mapf(clamp(frontDistance, 10, 20), 20, 10, 35, 30));
      } else {
        motor(30);
        delay(500);
        motor(0);
        while (true)
          ;
      }
      break;

    case 5:
      if (count_line >= 13 && count_line < 12 + parkingsection) {
        motor_and_steer(pidOutput);
        ultra_servo(pvYaw, TURN);
      } else {
        parking_step = 1;
      }
      break;

    default:
      motor_and_steer(final_degree);
      ultra_servo(pvYaw, ULTRA_DIR);
      if (count_line > 12 && parkingsection != -1) {
        parking_step = 5;
      }
      break;
  }
```
This `switch` statement controls the robot's parking process based on the value of `parking_step`, dividing it into multiple stages:
  Case 1: The robot begins by detecting parking conditions. If the purple blob (signature 3) isn’t detected or is too small (`purple_blob1.width` < 70), it adjusts the servo and ultrasonic direction, moving forward. When the condition changes, it moves to step 2.
  Case 2: The robot aligns itself. A timer (`halt_detect_parking`) tracks the duration, and the robot steers using `final_degree` while moving forward for 1400 milliseconds. Then, it advances to step 3, adjusting the turning angle (`plus_degree`) based on the direction that the robot turns.
  Case 3: The robot starts reversing for 2000 milliseconds, centering the steering and ultrasonic servos. Afterward, it proceeds to step 4.
  Case 4: The robot parks by steering based on `frontDistance`. If the distance is greater than 10, it adjusts steering and speed using a mapped value. Once close enough, it stops, waits 
  briefly.
  Case 5: The robot ensures it aligns properly in the parking section. It adjusts motors and servos while tracking the line count. Once done, it resets to step 1 for further operation.
  But if no specific step applies, the robot moving as usual. If a parking section is found and the line count exceeds 12, it transitions to step 5.

<br><hr>

### Function

This is all the function of our program

### `Initialize Everything`

```c++
void initialize_everything() {
  Serial.begin(19200);
  Serial1.begin(19200);
  Serial2.begin(19200);
  Serial3.begin(19200);

  compassPID.Start(0, 0, 0);
  compassPID.SetOutputLimits(-180, 180);
  compassPID.SetSampleTime(10);

  pinMode(STEER_SRV, OUTPUT);
  pinMode(ULTRA_SRV, OUTPUT);
  pinMode(ULTRA_PIN, INPUT);
  pinMode(RED_SEN, INPUT);
  pinMode(BLUE_SEN, INPUT);
  pinMode(BUTTON, INPUT);

  initMotor();
  while (!Serial)
    ;
  myservo.attach(ULTRA_SRV, 500, 2400);
  myservo2.attach(STEER_SRV, 500, 2500);
  steering_servo(0);
  ultra_servo(0, 'U');
}
```
The `initialize_everything` function sets up the robot by initializing serial ports, starting the compass PID controller with limits of -180° to 180°, and configuring pins for servos, sensors, and a button. It calls initMotor for motor setup, attaches servos with defined ranges, and resets them to default positions, ensuring the robot is ready to operate.

### `Degrees to radians`

```c++
float degreesToRadians(double degrees) {
  return degrees * PI / 180.0;
}

float radiansToDegree(double raidans) {
  return raidans / PI * 180.0;
}
```
These functions convert angles between degrees and radians.

### `Avoidance Calculation(based on size and position)`

```c++
float _cal_avoidance(char mode, int targetWidth, int objectWidth, int blockCenterX, int blockCenterY) {
  float focalLength = 2.8;
  float cameraFOV = 70;

  float distance = (targetWidth * focalLength * 100) / objectWidth;

  float deltaX = blockCenterX - (320 / 2);
  float deltaY = blockCenterY - (240 / 2);

  float detected_degree = -deltaX * cameraFOV / 320.0;

  float blockPositionX = distance * sin(degreesToRadians(detected_degree));
  float blockPositionY = distance * cos(degreesToRadians(detected_degree)) - 10;

  ULTRA_DIR = mode;

  if (mode == 'L') {
    return max(radiansToDegree(atan2(blockPositionX + (targetWidth / 2 + 10), blockPositionY)), 5) * 1.1;
  } else if (mode == 'R') {
    return min(radiansToDegree(atan2(blockPositionX - (targetWidth / 2 + 10), blockPositionY)), -5) * 0.9;
  } else {
    return 0;
  }
}
```
The `_cal_avoidance` function calculates the robot's avoidance angle based on the object's size and position. We use the camera's focal length and field of view to estimate the object's distance, then calculates the X and Y positions. Depending on whether the robot needs to turn left or right, we use trigonometry to compute the avoidance angle.

### `Avoidance Calculation(based on signature)`

```c++
float calculate_avoidance(int signature, int objectWidth, int blockCenterX, int blockCenterY) {
  int avoidance_degree = 0;

  if (signature == 2) {
    avoidance_degree = _cal_avoidance('L', 5, objectWidth, blockCenterX, blockCenterY);
  } else if (signature == 1) {
    avoidance_degree = _cal_avoidance('R', 5, objectWidth, blockCenterX, blockCenterY);
  } else if (signature == 3 || signature == 4) {
    avoidance_degree = _cal_avoidance(TURN, 20, objectWidth, blockCenterX, blockCenterY);
  }
  return avoidance_degree;
}
```
The `calculate_avoidance` function determines the robot's avoidance direction based on the object's signature. For green (signature 2), it calculates a left turn; for red (signature 1), a right turn. For purple (signatures 3 and 4), it uses the robot's turn direction, if it turns right it avoids to the right. If it turns left, it avoids to the left.

### `Wrap value`

```c++
int wrapValue(int value, int minValue, int maxValue) {
  int range = maxValue - minValue + 1;
  if (value < minValue) {
    value += range * ((minValue - value) / range + 1);
  }
  return minValue + (value - minValue) % range;
}
```
The `wrapValue` function adjusts a value to keep it within a specified range. If the value is below the minimum, it wraps around to the top of the range. Similarly, if the value exceeds the maximum, it wraps back around to the bottom. This ensures the value always stays within the `minValue` and `maxValue` range.

### `Initiate motor`

```c++
void initMotor() {
  int i;
  for (i = 0; i < MotorNum; i++) {
    digitalWrite(MotorPin[i].enPin, LOW);

    pinMode(MotorPin[i].enPin, OUTPUT);
    pinMode(MotorPin[i].directionPin, OUTPUT);
  }
}
```
The `initMotor` function initializes the motors by setting up their pins. It loops through all motors and configures their enable and direction pins as output, while also setting their enable pins to LOW.

### `Set motor direction`

```c++
void setMotorDirection(int motorNumber, int direction) {
  digitalWrite(MotorPin[motorNumber].directionPin, direction);
}
```
The `setMotorDirection` function sets the direction of a specific motor by adjusting its direction pin to either forward or backward.

### `Set motor speed`

```c++
inline void setMotorSpeed(int motorNumber, int speed) {
  analogWrite(MotorPin[motorNumber].enPin, 255.0 * (speed / 100.0));
}
```
The `setMotorSpeed` function adjusts the motor's speed by using `analogWrite` to control the enable pin's duty cycle. It converts the given speed (from 0 to 100) to a value between 0 and 255, with 255 representing full speed.

### `Motor`

```c++
void motor(int speed) {
  if (speed > 0) {
    setMotorDirection(M1, Forward);
    setMotorSpeed(M1, speed);
  } else {
    setMotorDirection(M1, Backward);
    setMotorSpeed(M1, speed);
  }
}
```
The `motor` function controls the motor's movement. If the speed is positive, it sets the motor to move forward; if negative, it sets the motor to move backward.

### `Color detection`

```c++
void color_detection() {
  int blue_value = analogRead(BLUE_SEN);
  if (TURN == 'U') {
    int red_value = analogRead(RED_SEN);
    if (blue_value < 600 || red_value < 600) {
      int lowest_red_sen = red_value;
      long timer_line = millis();
      while (millis() - timer_line < 100) {
        int red_value = analogRead(RED_SEN);
        if (red_value < lowest_red_sen) {
          lowest_red_sen = red_value;
        }
      }
      if (lowest_red_sen > 600) {
        TURN = 'L';
        plus_degree += 90;
      } else {
        TURN = 'R';
        plus_degree -= 90;
      }
      halt_detect_line_timer = millis();
      count_line++;
    }
  } else {
    if (millis() - halt_detect_line_timer > 1800) {
      if (blue_value < 600) {
        if (TURN == 'R') {
          plus_degree -= 90;
        } else {
          plus_degree += 90;
        }
        halt_detect_line_timer = millis();
        count_line++;
      }
    }
  }
}
```
This function works on the direction that the robot goes during the round. First, if red sensor value is more than 600 and blue's is less than 600, it means that it found red line, so it has to turn right. If both of the sensor's value is less than 600, it means that it found blue line and has to turn left. The robot stores this data and next time it sees a line after 1.8 seconds, it turns the same direction.

### `Steering servo`

```c++
void steering_servo(int degree) {
  myservo2.write((90 + max(min(degree, 50), -50)) / 2);
}
```
The function controls the steering servo's position. It takes a degree value, clamps it within the range of -50 to 50, and then adjusts it to fit the servo's expected range by adding 90 and dividing by 2.

### `Ultrasonic Servo`

```c++
void ultra_servo(int degree, char mode_steer) {
  int middle_degree = 0;
  if (mode_steer == 'F') {
    middle_degree = 150;
  } else if (mode_steer == 'R') {
    middle_degree = 225;
  } else if (mode_steer == 'L' || mode_steer == 'U') {
    middle_degree = 80;
  } else {
  }
  myservo.write(mapf(max(min(middle_degree + degree, 225), 45), 0, 270, 0, 180));
}
```
The `ultra_servo` function controls the ultra servo based on the given degree and steering mode. It first sets a middle degree based on the `mode_steer` parameter: 'F' sets it to 150, 'R' to 225, and 'L' or 'U' to 80. Then, it adjusts the servo position by adding the input degree to this middle degree.

### `Get distance`

```c++
float getDistance() {
  float raw_distance = mapf(analogRead(ULTRA_PIN), 0, 1023, 0, 500);
  if (TURN == 'L') {
    raw_distance += 0;
  } else if (TURN == 'R') {
    raw_distance -= 0;
  }
  return min(raw_distance, 50);
}

float getDistanceII() {
  float raw_distance = mapf(analogRead(ULTRA_PIN_II), 0, 1023, 0, 500);
  if (TURN == 'L') {
    raw_distance += 0;
  } else if (TURN == 'R') {
    raw_distance -= 0;
  }
  return min(raw_distance, 50);
}
```
The `getDistance` and `getDistanceII` functions measure the distance using ultrasonic sensors. Both functions use `analogRead` to get a sensor value, then map it to a distance range (0 to 500). The final distance is capped at a maximum of 50 units using `min`.

### `Get IMU`

```c++
bool getIMU() {
  while (Serial1.available()) {
    rxBuf[rxCnt] = Serial1.read();
    if (rxCnt == 0 && rxBuf[0] != 0xAA) return;
    rxCnt++;
    if (rxCnt == 8) {
      rxCnt = 0;
      if (rxBuf[0] == 0xAA && rxBuf[7] == 0x55) {
        pvYaw = (int16_t)(rxBuf[1] << 8 | rxBuf[2]) / 100.f;
        pvYaw = wrapValue(pvYaw + plus_degree, -179, 180);
        return true;
      }
    }
  }
  return false;
}
```
The `getIMU` function reads data from the Serial1 interface, expecting a specific format for communication with the IMU. It stores incoming bytes in the `rxBuf` array. The yaw value is then adjusted by adding `plus_degree` and wrapped within the range of -179 to 180 degrees using the `wrapValue` function.

### `Zero Yaw`

```c++
void zeroYaw() {
  Serial1.begin(115200);
  delay(100);
  Serial1.write(0XA5);
  delay(10);
  Serial1.write(0X54);
  delay(100);
  Serial1.write(0XA5);
  delay(10);
  Serial1.write(0X55);
  delay(100);
  Serial1.write(0XA5);
  delay(10);
  Serial1.write(0X52);
  delay(100);
}
```
The `zeroYaw` function is used to reset or calibrate the yaw value of the IMU (Inertial Measurement Unit).

### `Motor and Steering`

```c++
void motor_and_steer(int degree) {
  degree = clamp(degree, -52, 52);
  steering_servo(degree);
  motor((map(abs(degree), 0, 30, 49, 49)));
}
```
The `motor_and_steer` function adjusts the robot's steering by clamping the degree between -52 and 52, then sets the servo position. It also controls the motor speed, setting it to 49 based on the absolute value of the degree.

### `Clamp`

```c++
float clamp(float value, float minVal, float maxVal) {
  if (value < minVal) return minVal;
  if (value > maxVal) return maxVal;
  return value;
}
```
The `clamp` function limits a given value to stay within the range specified by `minVal` and `maxVal`. If the value is smaller than `minVal`, it returns `minVal`; if it's larger than `maxVal`, it returns `maxVal`; otherwise, it returns the original value.

### `Check LEDs`

```c++
void check_leds() {
  while (true) {
    Serial.print("Geen: ");
    Serial.print(analogRead(BLUE_SEN));
    Serial.print("   Red: ");
    Serial.println(analogRead(RED_SEN));
  }
}
```
This function is for checking sensors value.

### `Angle Difference`

```c++
float angleDiff(float a, float b) {
  float diff = a - b;
  while (diff > 180) diff -= 360;
  while (diff <= -180) diff += 360;
  return diff;
}
```
The `angleDiff` function calculates the difference between two angles a and b, ensuring the result is within the range of -180° to 180°. If the difference exceeds these limits, it wraps around by adding or subtracting 360° to keep the result within the expected range.

<br><hr>

### OpenMV

- #### **Section 1 [OpenMV]**

```c++
import time
import sensor
import display
from pyb import UART
```
The code imports libraries for time delays, sensor handling, display management, and UART communication, typically used in microcontroller projects with cameras and displays.

- #### **Section 2 [OpenMV]**

```c++
# Initialize sensor
sensor.reset()
sensor.set_pixformat(sensor.RGB565)
sensor.set_framesize(sensor.QVGA)  # 320x240 resolution

sensor.skip_frames(time=2000)  # Wait for settings to take effect.

# Lock auto-exposure and auto-white-balance to prevent drift across reboots.
sensor.set_auto_gain(False)  # Disable auto gain.
sensor.set_auto_whitebal(False)  # Disable auto white balance.

# Lock exposure to prevent fluctuations in lighting conditions.
sensor.set_auto_exposure(False, exposure_us=7000)  # Adjust exposure manually.

sensor.set_contrast(3)
sensor.set_brightness(0)
sensor.set_saturation(0)

sensor.skip_frames(time=1000)

#sensor.__write_reg(0x0E, 0b00000000)  # Disable night mode
#sensor.__write_reg(0x3E, 0b00000000)  # Disable BLC
```
This code configures the sensor with fixed settings: RGB565 format, QVGA resolution (320x240), manual exposure, and disabled auto-gain and white balance. It also adjusts contrast, brightness, and saturation for stable imaging.

- #### **Section 3 [OpenMV]**

```c++
# Color thresholds
GREEN_THRESHOLDS = [(22, 48, -52, -21, 17, 49)]
RED_THRESHOLDS = [(0, 52, 13, 37, -3, 25)]
PURPLE_THRESHOLDS = [(33, 70, -25, 14, 42, 76)]
```
These threshold values define color ranges for detecting green, red, and purple objects based on the HSV color model

- #### **Section 4 [OpenMV]**

```c++
# Region of Interest (ROI)
ROI = (0, 160, 320, 240)

# Initialize UART
uart = UART(3, 19200, timeout_char = 2000)
clock = time.clock()
```
This code initializes the Region of Interest (ROI) for image processing and sets up the UART communication at a baud rate of 19200 with a timeout of 2000 milliseconds. The clock is also initialized to manage timing for the processing loop.

- #### **Section 5 [OpenMV]**

```c++
def send_blob_data(blob, blob_type, color):
    img.draw_rectangle(blob.rect(), color=color)
    img.draw_cross(blob.cx(), blob.cy(), color=color)
    data = f"{blob.cx()},{blob.cy()},{blob.w()},{blob.h()},{blob_type}\n"
    uart.write(data)
    print(data)
```
This function `send_blob_data` processes and sends information about a detected blob over UART. It draws a rectangle and a cross on the image at the blob's coordinates, using the specified color. The blob's position (cx, cy), size (width, height), and type are formatted as a string and sent via `UART.v`.

- #### **Section 6 [OpenMV]**

```c++
def send_no_blob_data():
    data = "0,0,0,0,0\n"
    uart.write(data)
    print(data)
```
The `send_no_blob_data` function sends a default "no blob" data string over UART. It indicates that no blob was detected by setting all blob-related values (position, size, and type) to zero.

- #### **Section 7 [OpenMV]**

```c++
while True:
    clock.tick()
    img = sensor.snapshot()

    # Detect red and green blobs
    green_blobs = img.find_blobs(GREEN_THRESHOLDS, roi=ROI, area_threshold=30, pixels_threshold=30, merge=True)
    red_blobs = img.find_blobs(RED_THRESHOLDS, roi=ROI, area_threshold=30, pixels_threshold=30, merge=True)

    # Find the largest blob between red and green blobs
    largest_green = max(green_blobs, key=lambda b: b.area(), default=None)
    largest_red = max(red_blobs, key=lambda b: b.area(), default=None)

    # Determine the largest blob between red and green
    largest_blob = None
    if largest_green and largest_red:
        largest_blob = largest_green if largest_green.area() > largest_red.area() else largest_red
    elif largest_green:
        largest_blob = largest_green
    elif largest_red:
        largest_blob = largest_red

    # Send data for the largest red or green blob (if found), else send '0'
    if largest_blob:
        blob_type = 2 if largest_blob in green_blobs else 1  # Green = 2, Red = 1
        color = (0, 255, 0) if blob_type == 2 else (200, 0, 0)
        send_blob_data(largest_blob, blob_type, color)
    else:
        send_no_blob_data()  # Send 0 when no red or green blobs are found

    # Detect and send data for all purple blobs
    purple_blobs = img.find_blobs(PURPLE_THRESHOLDS, roi=ROI, area_threshold=30, pixels_threshold=30, merge=True)
    purple_blobs = sorted(purple_blobs, key=lambda b: b.cx())

    if purple_blobs:
        for i, purple_blob in enumerate(purple_blobs):
            color = (255, 0, 255) if i == 0 else (252, 244, 3)  # Alternate colors for blobs
            send_blob_data(purple_blob, 3 + i, color)  # Different blob types for each purple blob
    cropped_img = img.crop(roi=ROI)  # Crop to exclude the top 120 pixels
    # Optional: Read and print incoming UART data
    if uart.any():
        data = uart.readline()
        print("Received:", data)

```
This code captures images, detects red, green, and purple blobs, and sends their data via UART. It finds the largest green or red blob and sends its position and size, drawing a rectangle and cross on the image. If no blobs are found, a "no blob" signal is sent. Purple blobs are also detected and sent with alternating colors and types. The image is cropped to focus on the lower half, and incoming UART data is printed when received. This loop enables real-time object tracking.

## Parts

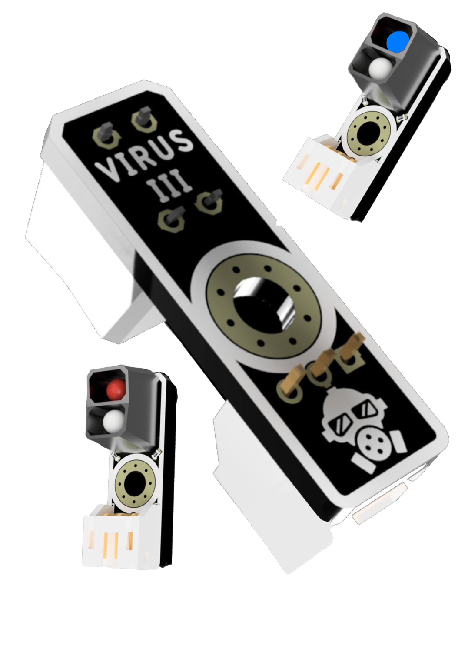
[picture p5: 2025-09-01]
Robot-Photos/Robot Parts/Power Management And Inspection/Red sensor.png

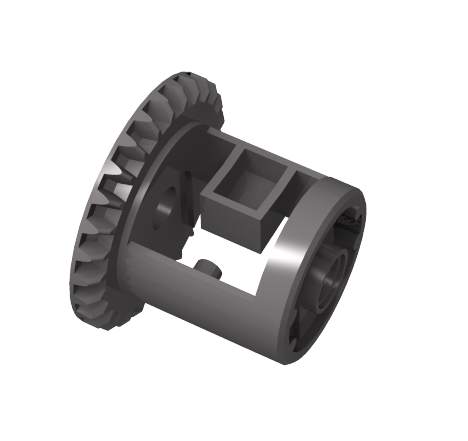
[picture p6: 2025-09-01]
Robot-Photos/Robot Parts/Movement/differential gear.png

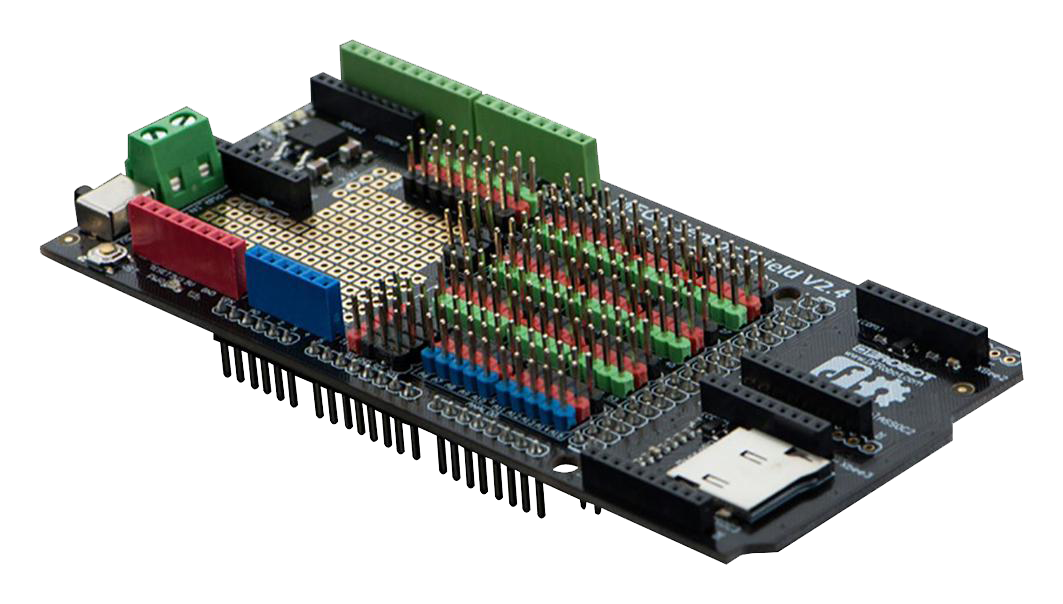
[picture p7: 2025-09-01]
Robot-Photos/Robot Parts/Controller/Sensor shield.png

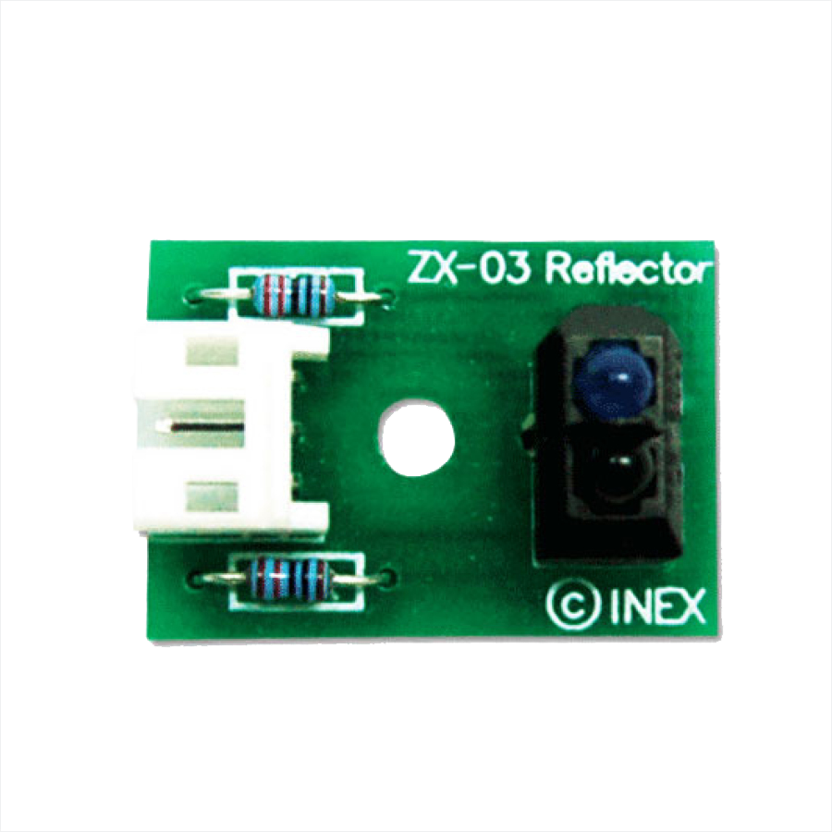
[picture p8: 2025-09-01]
Robot-Photos/Robot Parts/Power Management And Inspection/Blue sensor.png

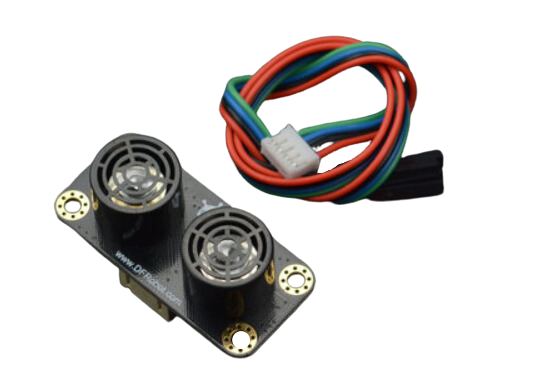
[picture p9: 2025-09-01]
Robot-Photos/Robot Parts/Power Management And Inspection/Ultrasonic.png

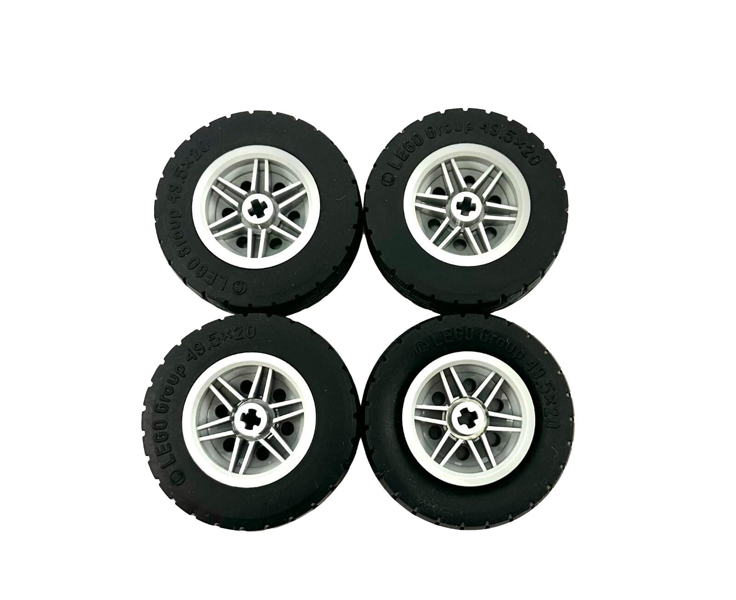
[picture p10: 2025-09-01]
Robot-Photos/Robot Parts/Movement/Wheels.png

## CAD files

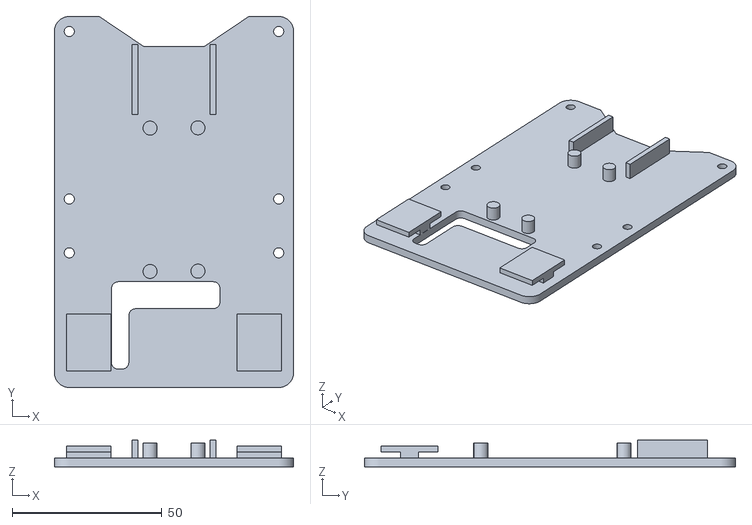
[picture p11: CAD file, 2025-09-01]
3D_Models/Main Base.stl
80.0 x 124.0 x 9.00

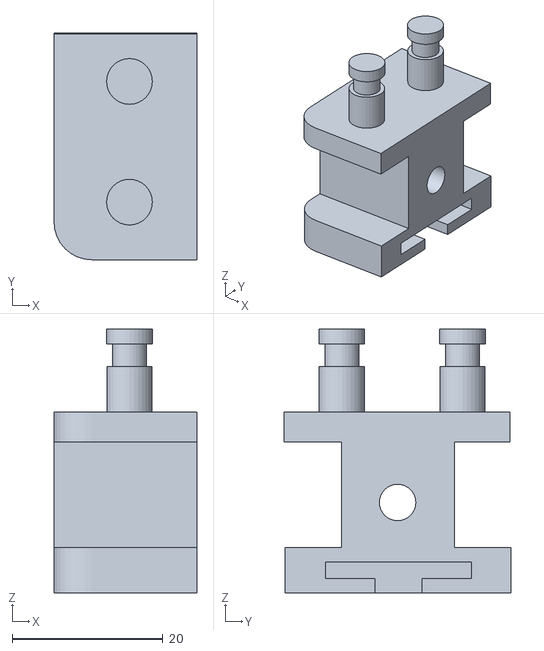
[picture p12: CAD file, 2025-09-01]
3D_Models/Left Differential Gear Mount.stl
19.0 x 30.0 x 35.0

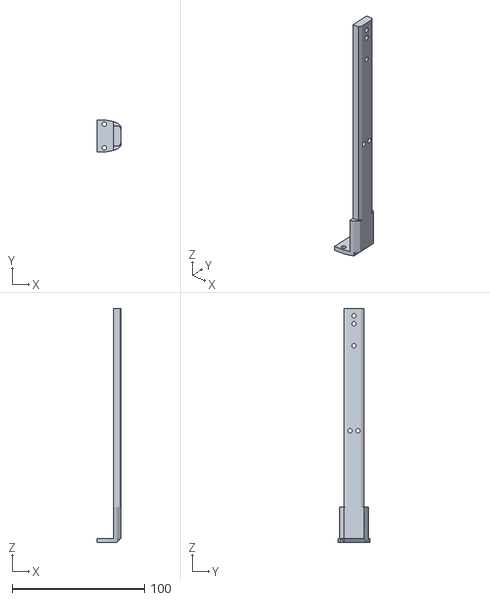
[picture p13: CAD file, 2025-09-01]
3D_Models/Right Side Handle Support.stl
18.0 x 23.9 x 177.0

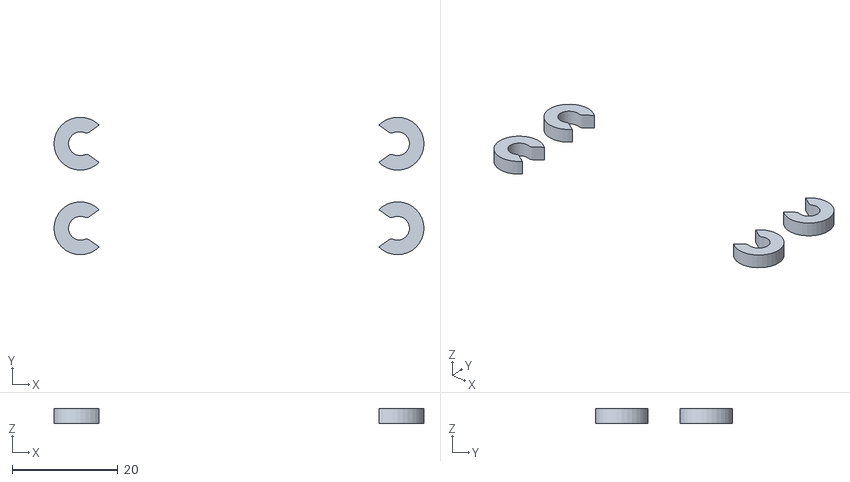
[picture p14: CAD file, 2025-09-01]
3D_Models/C Clip x4.stl
70.0 x 26.0 x 2.90

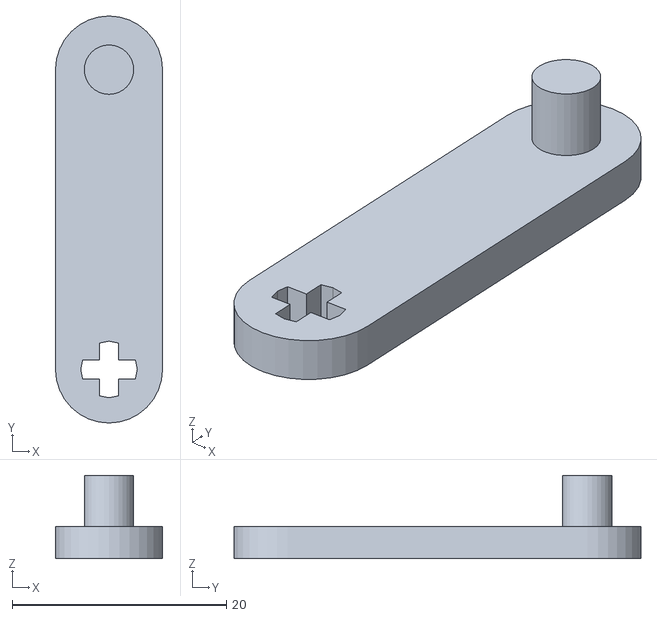
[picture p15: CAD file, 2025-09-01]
3D_Models/Steering Linkage Arm.stl
10.0 x 38.0 x 7.75

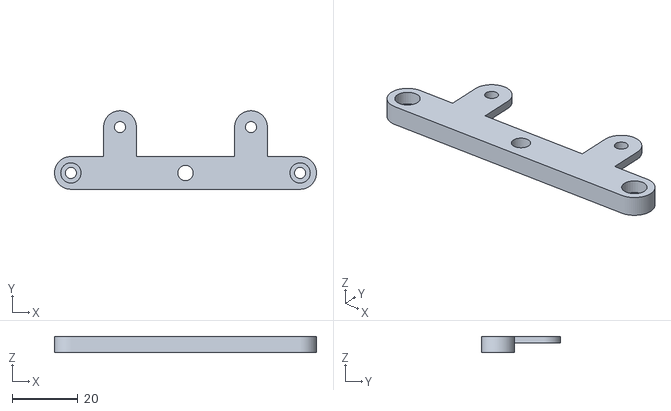
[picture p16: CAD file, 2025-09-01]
3D_Models/Bottom Steering Mount.stl
80.0 x 24.0 x 5.00

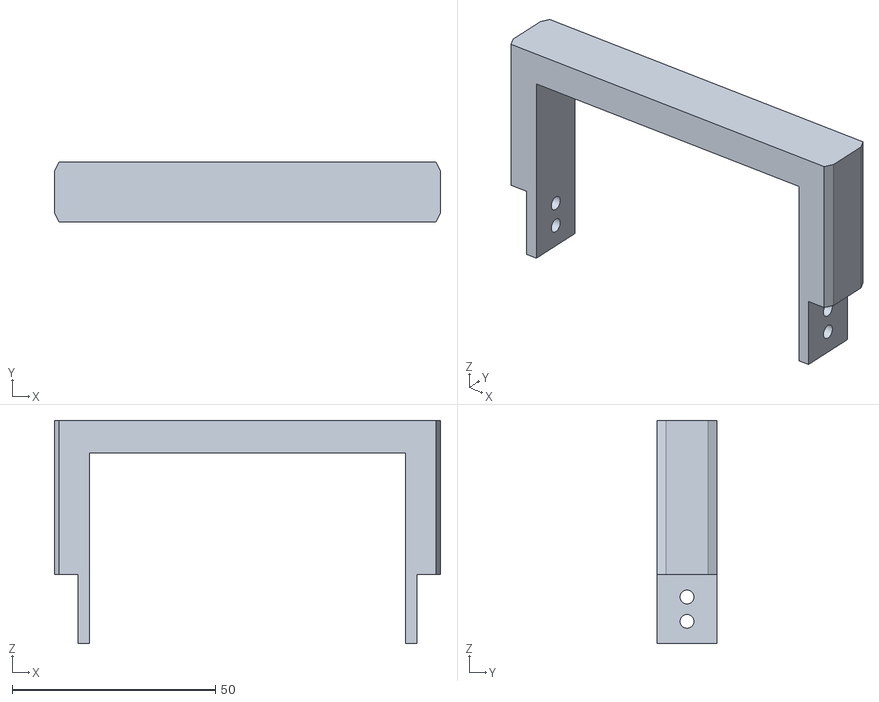
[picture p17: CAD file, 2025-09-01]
3D_Models/Upper Handle Bracket.stl
95.0 x 14.7 x 55.0

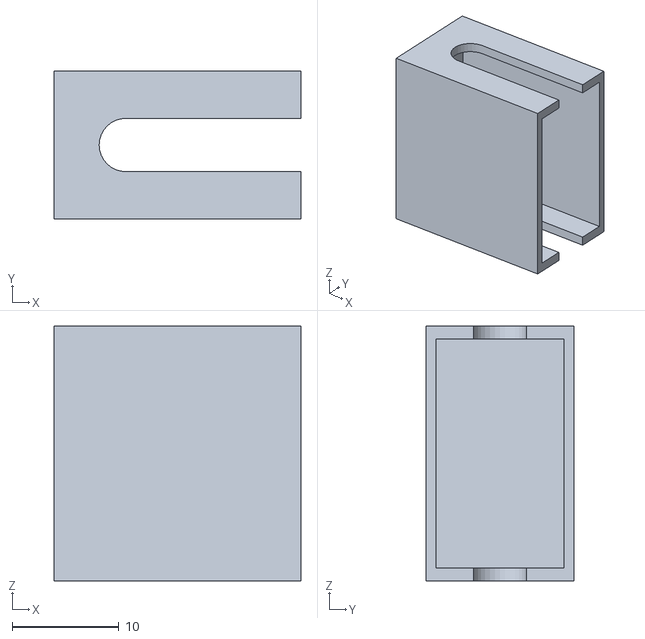
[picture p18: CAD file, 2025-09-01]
3D_Models/Switch Box.stl
23.2 x 13.9 x 23.9

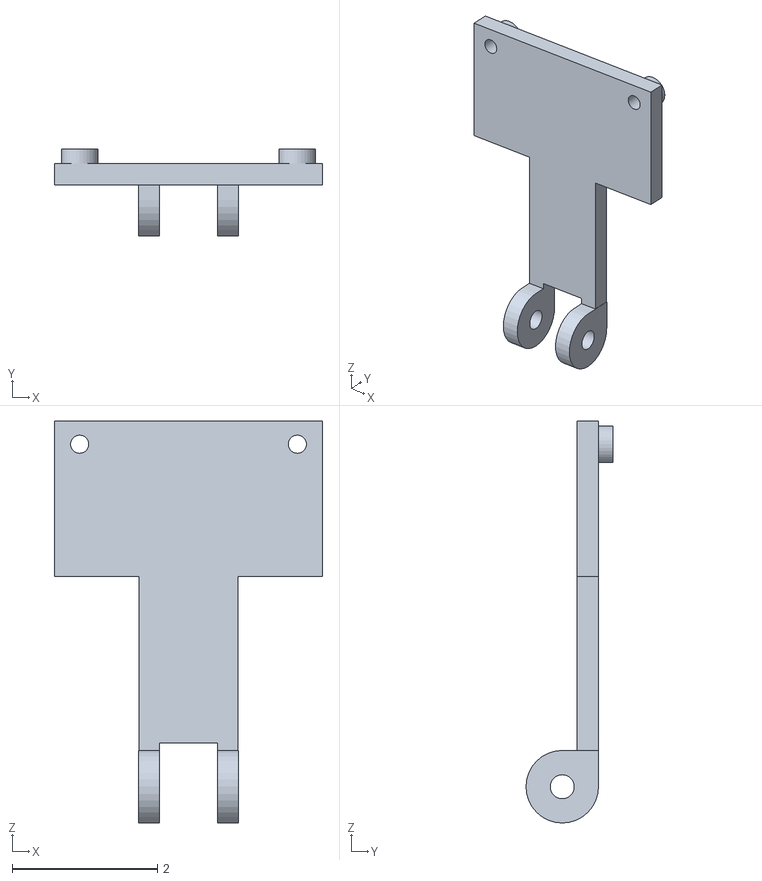
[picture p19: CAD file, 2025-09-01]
3D_Models/Camara Plate.stl
3.70 x 1.20 x 5.54

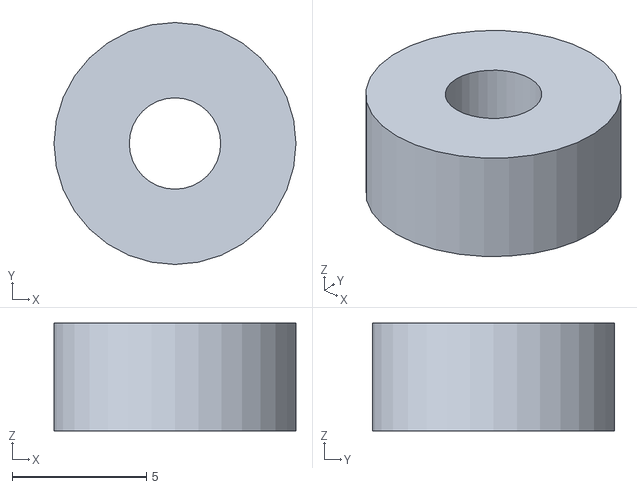
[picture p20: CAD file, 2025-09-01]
3D_Models/Steering Arm Support.stl
9.00 x 9.00 x 4.00

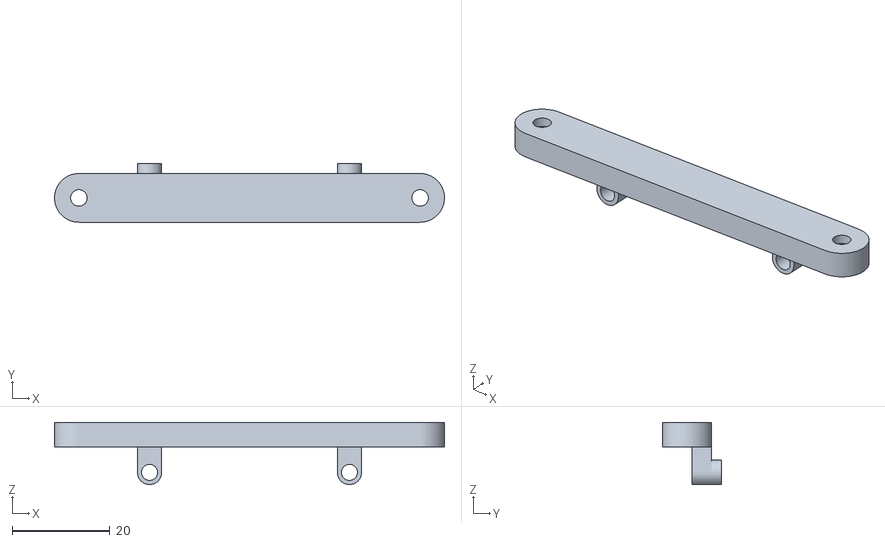
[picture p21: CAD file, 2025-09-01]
3D_Models/Top Steering Mount.stl
80.0 x 12.0 x 12.8

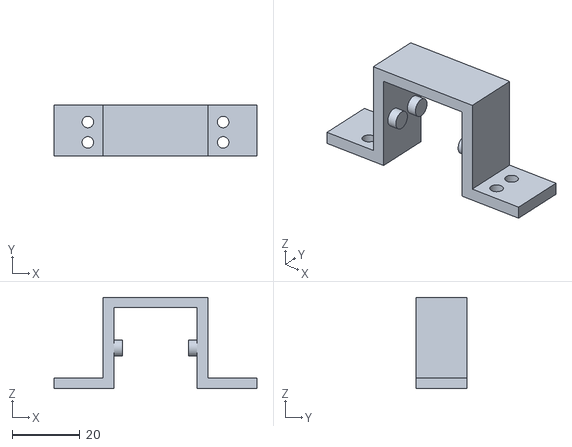
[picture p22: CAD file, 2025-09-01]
3D_Models/Servo Bracket.stl
60.0 x 15.0 x 27.0

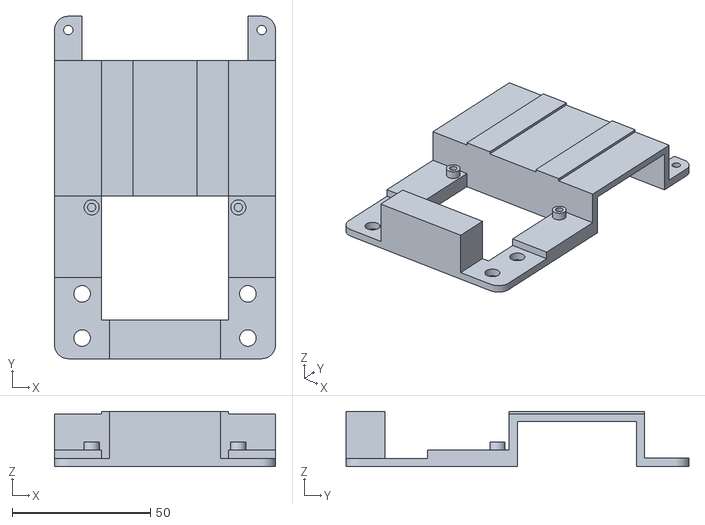
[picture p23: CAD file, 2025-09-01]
3D_Models/Power Tray.stl
80.0 x 124.0 x 20.0

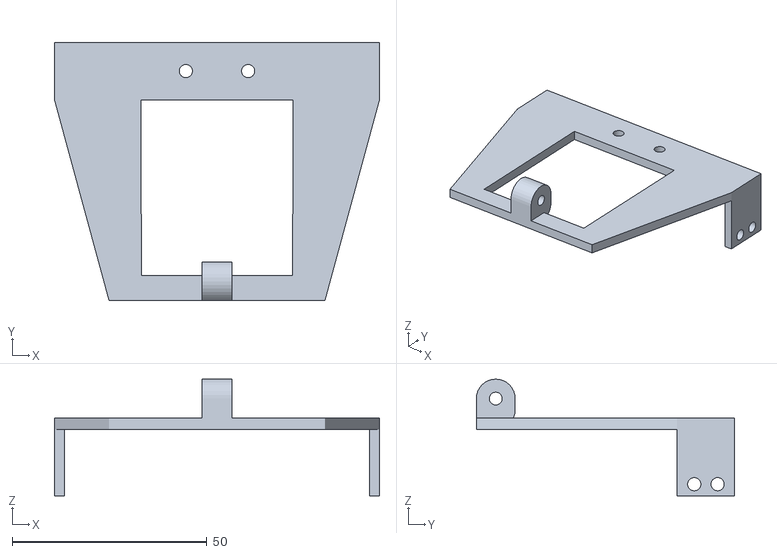
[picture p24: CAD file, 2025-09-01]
3D_Models/Gyro-Camara Mount.stl
83.5 x 66.4 x 30.0

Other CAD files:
3D_Models/Right Differential Gear Mount.stl
3D_Models/Support Plate.stl
3D_Models/Left Side Handle Support.stl
3D_Models/Steering Arm.stl

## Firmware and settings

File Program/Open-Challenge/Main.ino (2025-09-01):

#include "Mapf.h"
#include "Servo.h"
#include <PID_v2.h>

Servo myservo1;
Servo myservo2;

//  Compass Variables
float pvYaw, pvRoll, pvPitch;
uint8_t rxCnt = 0, rxBuf[8];

//  Motor B
const int E1Pin = 10;
const int M1Pin = 12;
const int E2Pin = 11;
const int M2Pin = 13;

/**inner definition**/
typedef struct {
  byte enPin;
  byte directionPin;
} MotorContrl;

const int M1 = 0;
const int MotorNum = 1  ;

const MotorContrl MotorPin[] = { {E1Pin, M1Pin}, {E2Pin, M2Pin} } ;

const int Forward = LOW;
const int Backward = HIGH;

//  Servos
int const STEER_SRV = 23;
int const ULTRA_SRV = 16;

//  Ultrasonic Sensor
int const ULTRA_PIN = A9;

//  Light Sensors
int const RED_SEN = A6;
int const GEEN_SEN = A7;

//  Button
int const BUTTON = A8;

char TURN = 'U';
int compass_offset = 0;
long halt_detect_line_timer;
bool found_block = false;
int Servo_Value;
int x = 1;
int Y = 20;
int count = 0;

// Specify the links and initial tuning parameters
PID_v2 compassPID(0.4, 0.0001, 0.025, PID::Direct);

void setup() {
  compassPID.Start(0, 0, 0);
  compassPID.SetOutputLimits(-180, 180);
  compassPID.SetSampleTime(10);
  pinMode(E1Pin, OUTPUT);
  pinMode(M1Pin, OUTPUT);
  pinMode(STEER_SRV, OUTPUT);
  pinMode(ULTRA_SRV, OUTPUT);
  pinMode(ULTRA_PIN, INPUT);
  pinMode(RED_SEN, INPUT);
  pinMode(GEEN_SEN, INPUT);
  pinMode(BUTTON, INPUT);
  Serial.begin(9600);
  initMotor();
  myservo1.attach(STEER_SRV, 600, 2400);
  myservo2.attach(ULTRA_SRV, 600, 2400);
  steering_servo(0);
  ultra_servo(0, 'L');
  // check_leds();
  while (analogRead(BUTTON) > 500)
    ;
  zeroYaw();
  while (analogRead(BUTTON) <= 500)
    ;
}

void loop() {
  // getIMU();
  // Serial.println(pvYaw);
  // //(❁´◡`❁);
  

  while (analogRead(BUTTON) > 500) {
    getIMU();
    line_detection();
    int wall_distance = getDistance();
    motor_and_steer((1 * x) * compassPID.Run((x * pvYaw) + ((wall_distance - Y)) * ((float(TURN == 'TURN') - 0.5) * 2)) * -1);
    ultra_servo(pvYaw,TURN);
    if (count >= 12) {
      long timer01 = millis();
      while (millis() - timer01 < 850) {
        getIMU();
        line_detection();
        motor_and_steer((1 * x) * compassPID.Run((x * pvYaw) + ((wall_distance - Y)) * ((float(TURN == 'TURN') - 0.5) * 2)) * -1);
        ultra_servo(pvYaw,TURN);
      }
      setMotorSpeed( M1 , 0 );
      while (true) {
      }
    }
  }
    setMotorSpeed( M1 , 0 );
  while (analogRead(BUTTON) <= 500)
    ;
  while (analogRead(BUTTON) > 500)
    ;
  while (analogRead(BUTTON) <= 500)
    ;
}
